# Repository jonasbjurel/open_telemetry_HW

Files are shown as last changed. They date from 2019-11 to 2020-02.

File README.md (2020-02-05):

# open_telemetry_HW





**Licenses:**

The official OpenFly Telemetry project(s) are all open source. The licensing may vary from GPL 2, GPL 3, Apache, or Creative Commons. As with many other hardware projects – OpenFly Telemetry comes with the Creative Commons - CC BY 2.0 license.

**Disclaimers:**

The use of any HW, SW or instructions from the OpenFly Telemetry open source project, or any references to other art - is at your own risk. No warranties, or legal obligations shall be assumed from the creators – in any way. Flying model planes, drones or other remotely controlled vehicles always impose danger to the surroundings – make all necessary precautions to make sure that no one is in danger even in case the control of your model is lost for whatever reason.

# Latest news
OFT001v1P1A* with sample BIST SW have declared it's first release candidate February 04 - 2020. First prototype full release is expected during February 2020. See the Wiki for mor information: https://github.com/jonasbjurel/open_telemetry_HW/wiki

# WIKI
 https://github.com/jonasbjurel/open_telemetry_HW/wiki

# OpenFly Telemetry overview
OpenFly Telemetry is an open source project aiming to provide telemetry and navigation capabilities for model airplanes and drones through open source hardware and software. It uses various on-board sensor capabilities such as GPS, Accelerometers, Gyroscopes, Magnetometers, Pitot tubes, temperature sensors, battery voltage and current sensors, RPM sensors, etc. to provide the operator or algorithms with data for manual or automated corrective actions. The algorithms are some time autonomous and resides in the model, are sometimes on ground with the receiver or nearby connected devices or are sometimes even in distant clouds.
The OFT modules can also be placed in the module bay of the transmitter to enrich the transmitter awareness, e.g. Position, direction and additional communication capabilities such as Bluetooth and WIFI conectivity.
 
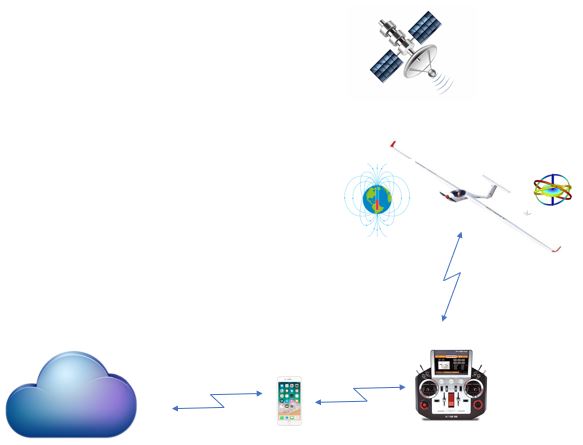
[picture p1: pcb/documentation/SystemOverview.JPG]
OpenFly Telemetry basic idea


**Figure 1:** OpenFly Telemetry basic idea

# OpenFly Telemetry (OFT) system description
OFT has two basic components: the Ada fruit ESP32 Huzzah feather processor board and the OFT system board. The ESP32 processor board obviously holds the software and algorithms for telemetry and navigation. The system board interfaces with the radio receiver and its telemetry and servo busses. The system is modular, and you can compose your choice of capabilities by stacking various OFT sensor boards on top of each other.

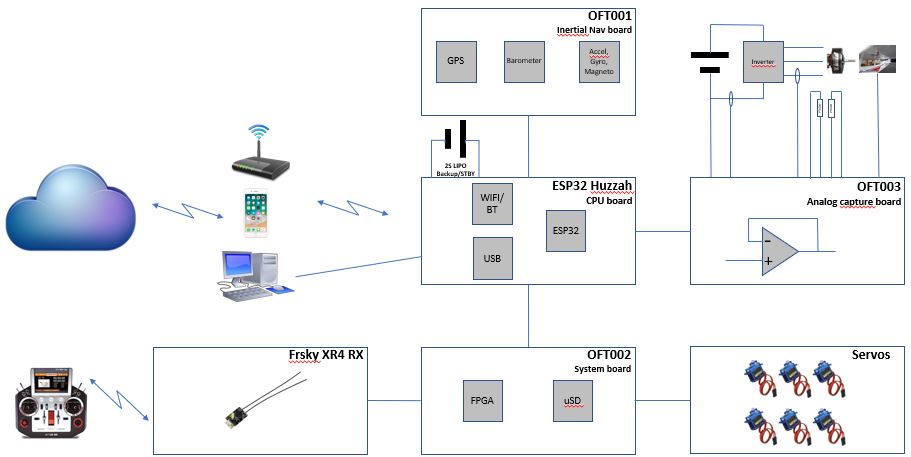
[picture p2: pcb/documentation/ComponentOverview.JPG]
OpenFly Telemetry system view


**Figure 2:** OpenFly Telemetry system view

OFT is based out of the Ada fruit ESP32 Huzzah feather processor board. This board hosts an ESP32 processor with two 32-bit general processor cores, 2 float processors and one ultra-low-power co-processor from Espressif (https://www.espressif.com/). Furthermore, the ESP32 board provides wireless connectivity through Bluetooth and WIFI as well as ensuring continuous power supply through an optional 2S designated LIPO, which could temporarily feed the servos and the receiver- should the main supply drain.
The ESP32 mother board connects to several telemetry acquisition boards in mother-daughter board/shield configurations.

Ada fruit ESP32 Huzzah feather board

**Figure 3:** Ada fruit ESP32 Huzzah feather board

For the on-board use cases (as opposed to the TX bay use case), the bottom most shield in the stack holds the OFT System board. The system board has an FPGA that connects to the radio receiver through the S.PORT for telemetry data, and the SBUS for servo output. The FPGA will allow the ESP32 processor to mix in servo corrections from the processor, transmitting upstream telemetry data, as well as receiving upstream telemetry and servo information from the transmitter. 
The system board interconnects with the radio control receiver through its S.PORT and SBUS.

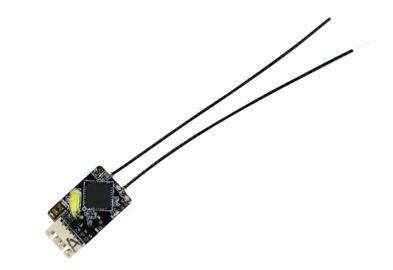
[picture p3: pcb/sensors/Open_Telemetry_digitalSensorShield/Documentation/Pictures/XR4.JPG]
Frsky XR4


**Figure 4:** Frsky XR4 2.4 GHz MIMO CDMA receiver with S.PORT- (telemetry) and SBUS (Servos) connections

# OpenFly Telemetry resources
## OpenFly Telemetry repositories
[OpenFly Telemetry main applications repository](https://github.com/jonasbjurel/open_telemetry)
This repository provides the application software repository for the OpenFly Telemetry project.

[OpenFly Telemetry hardware repository](https://github.com/jonasbjurel/open_telemetry_HW)
The repository for this project - providing HW blue-prints and designs for OpenFly Telemetry.

##  OpenFly Telemetry Dependencies
[ESP32 Arduino](https://github.com/espressif/arduino-esp32)
The Arduino port of Espressif ESP32.

[ESP32 FreeRTOS port documentation](https://docs.espressif.com/projects/esp-idf/en/latest/api-reference/system/freertos.html) FreeRTOS APIs and methods available for ESP32

[High availability- and embedded system FreeRTOS  shim layer](https://github.com/jonasbjurel/coreNoStopRTOS)
System initialization, process monitoring, memory management, system bus arbitration, inter process communication, and much more..

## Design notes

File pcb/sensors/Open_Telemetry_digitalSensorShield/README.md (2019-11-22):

# OFT001v1 Inertial navigation board 
The OFT001v1 Inertial navigation board captures navigational data, such as GPS positioning, 3D acceleration data, 3D Gyroscopic data, 3D Magnetic data, Barometric pressure, Temperature and Humidity. Those data are provided to the ESP32 processor card (and any other shield cards) through I2C and RS232. The data will be filtered, processed and transferred by the ESP32 card and the OFT System card FPGA. It is still to be seen if we can/will implement a high-performance Inertial navigation fuse fixed point Kalman filter in the FPGA, or if it is better done in SW?

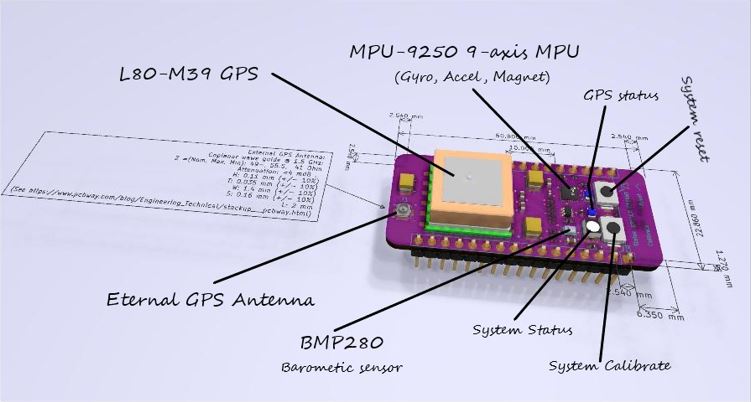
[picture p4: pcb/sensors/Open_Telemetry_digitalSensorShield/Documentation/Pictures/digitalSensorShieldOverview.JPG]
OFT001v1 Inertial navigation card overview

 
**Figure 5:** OFT001v1 Inertial navigation card overview

The OFT001v1 card has an L80-M39 GPS with a built-in patch antenna, and an optional connector for an external 50 Ohm active antenna; an MP-9250 3D axis for each of: Accelerometer, Gyroscope and Magnetometer; and a BMP280 Barometric pressure- humidity- and temperature sensor. Note that the axise's for the acelerometers and Gyrometers differs from those of the manetometers (x swaped with y, and neative Z), clearly marked on the board. The communication with these sensors have been segmented so that the MPU runs on its own high speed I2C channel, allowing fast updates, Kalman filtering-, integration- and Quaternion calculation cycles by the CPU (and possibly later offloaded by the OFT System card FPGA); the BMP280 is less latency critical, and shares an I2C channel with potentially other devices in the stack; while the GPS communication happens over an RS232 serial channel using extensions of the NMEA protocol.

There is one green LED indicator for GPS lock, one orange LED indictor for External GPS antenna use, and an RGB LED for generic system status indication driven from the ESP32 CPU board. There are also two push buttons: one which is connected to the overall system reset, and another multi-purpose push button intended for system calibration activities.

It is important that OFT001v1 sits on the top of the mother-daughter board stack (unless an external GPS antenna is used) in order to achieve a good GPS signal.
Cupper layers have been kept out from ESP32 Bluetooth and WIFI PCB antennas to not deteriorate the signal strength from those.

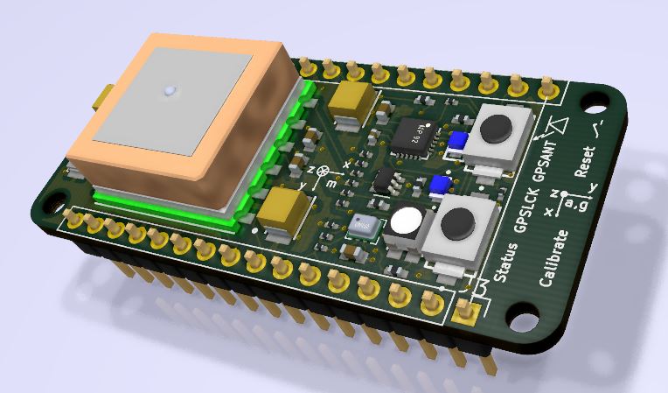
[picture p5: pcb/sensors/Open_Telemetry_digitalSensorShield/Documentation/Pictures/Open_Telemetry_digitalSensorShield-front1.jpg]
OFT001v1


**Figure 6:** OFT001v1

?
## OFT001v1 shield pin-out

| OFT001 12 pin header (J2) | ESP32 HUZZAH 12 pin header (JP3) | ESP32 silicon | Comments |
|---|---|---|---|
| 1 - N/C | VBAT | - | N/C |
| 2 - N/C | EN | - | N/C |
| 3 - N/C | VBUS | - | N/C |
| 4 – RED LED | IO13_A12 | 13 - IO13/A2_6| Red system status led  |
| 5 – BLUE LED | IO12_A11 | 14 – IO12/A2_5| Blue system status led |
| 6 – GREEN LED | IO27_A10 | 12 – IO27/A2_7| Green system status led|
| 7 - N/C | IO33_A9 | 9 - IO33/A1_5 | N/C |
| 8 - N/C | IO15_A8 | 23 – IO15/A2_3| N/C |
| 9 - N/C | IO32_A7 | 8 – IO32/A1_4 | N/C |
| 10 - N/C | IO14_A6 | 13 – IO14/A2_6| N/C |
| 11 - I2C_0_SCL_3V | SCL | 36 – IO22 | Common non-critical I2C|
| 12 - I2C_0_SDA_3V | SDA | 37 – IO23 | Common non-critical I2C|

**Table 1:** J2 shield pin connector

| OFT001 16 pin header (J3) | ESP32 HUZZAH 16 pin header (JP1) | ESP32 silicon |Comments |
|---|---|---|---|
| 1 – INT_0 | IO21 | 33 - IO21 | Interrupt from MPU9250 |
| 2 - I2C_1_SDA_3V | IO17 | 28 - IO17 | Critical MPU I2C |
| 3 - I2C_1_SCL_3V | IO16 | 27 - IO16 | Critical MPU I2C |
| 4 - N/C | MISO | 31 - IO19 | N/C |
| 5 - N/C | MOSI | 30 - IO18 | N/C |
| 6 - N/C | SCK | 29 - IO5 | N/C |
| 7 - CALIB | A5_IO4 | 26 - IO4/A2_2 | System calibration button |
| 8 - UART_1_CLIENT_RXD | A4_IO36 | 4 - IO36/A1_0 | L8-M39 GPS UART (NMEA) |
| 9 - UART_1_CLIENT_TXD | A3_I39 | 5 – IO39/A1_3 | L8-M39 GPS UART (NMEA) |
| 10 – N/C | A2_I34 | 6 – I34/A1_6  | N/C |
| 11 – N/C | A1_DAC1 | 10 – IO25/DAC1/A2_8| N/C |
| 12 – N/C | A0_DAC2 | 11 – IO26/DAC2/A2_9| N/C |
| 13 - GND | GND | -	 | GND from ESP32 motherboard|
| 14 – N/C | N/C | - | N/C |
| 15 - +3.3V (VDD) | +3.3V | - | 3.3V max 120 mA from ESP32 motherboard (rated for max ???)|
| 16 - RESET | RESET | 3 - EN | 2-Way reset |

**Table 2:** J3 shield pin connector

| OFT001 Ext GPS Ant. (J1) | Comments |
|---|---|
| 1 – AGND | External active GPS antenna ground |
| 2 – EXTANT | External active GPS antenna signal with VDD DC applied for power feed |

**Table 3:** J1 External PS Antenna

## OFT001v1 addressing

| I2CBus | Addr	 | Function | Comments |
|---|---|---|---|
| 0	 | 0x77(0x761) (1) | BME280 | - |
| 1 | 0x68(0x692) (2) | MPU9250  | - |

1)	Alternative address if NULL resistor R4 is mounted (not default)
2)	Alternative address if NULL resistor R7 is mounted (not default)

**Table 4:** OFT001v1 I2C addressing

## OFT001 v1 operating specifications
### Operational conditions:

| Parameter | Nom | Max | Min |
|---|---|---|---|
| Voltage | 3.3 V  | 3.6 V | 3.0 V |
| Current | 30 mA  | 120 mA  | - |
| Power dissipation  | 100 mW | 400 mW  | - |
| Ambient temp | - | 85 degC | -40 degC |

**Table 5:** OFT001v1 Operational conditions

### GPS antenna operational conditions:
The built in GPS patch antenna provides the following characteristics:

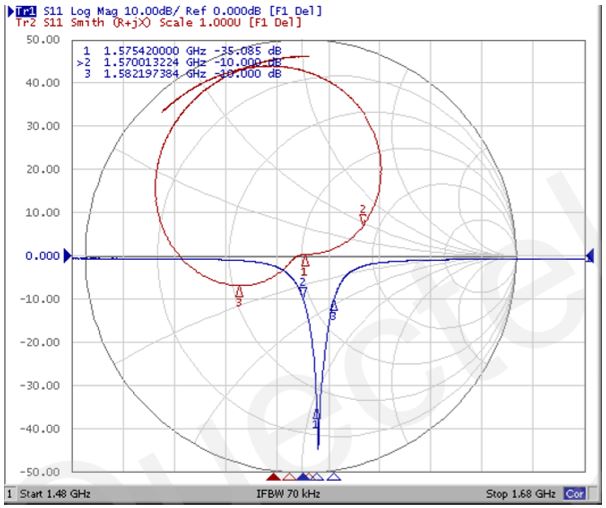
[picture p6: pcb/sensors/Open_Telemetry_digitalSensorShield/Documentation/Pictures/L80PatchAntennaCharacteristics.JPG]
GPS antenna characteristics


**Figure 7:** OFT001v1 Built in L80-M39 path GPS antenna characteristics

External GPS antenna operational requirements:

| Parameter | Value |
|---|---|
| DC feed: | 3.6V – 2.5V |
| DC current (max): | <??? |
| Center frequency: | 1575.42MHz |
| Band width: | >5MHz |
| VSWR: | <2 (Typ.) |
| Polarization: | RHCP or Linear |
| Noise figure: | <1.5dB |
| Gain (antenna): | >-2dBi |
| Gain (embedded LNA): | 20dB (Typ.) |
| Total gain: | >18dBi (Typ.)  |

**Table 6:** OFT001v1 External operational conditions

## OFT001v1 schematics

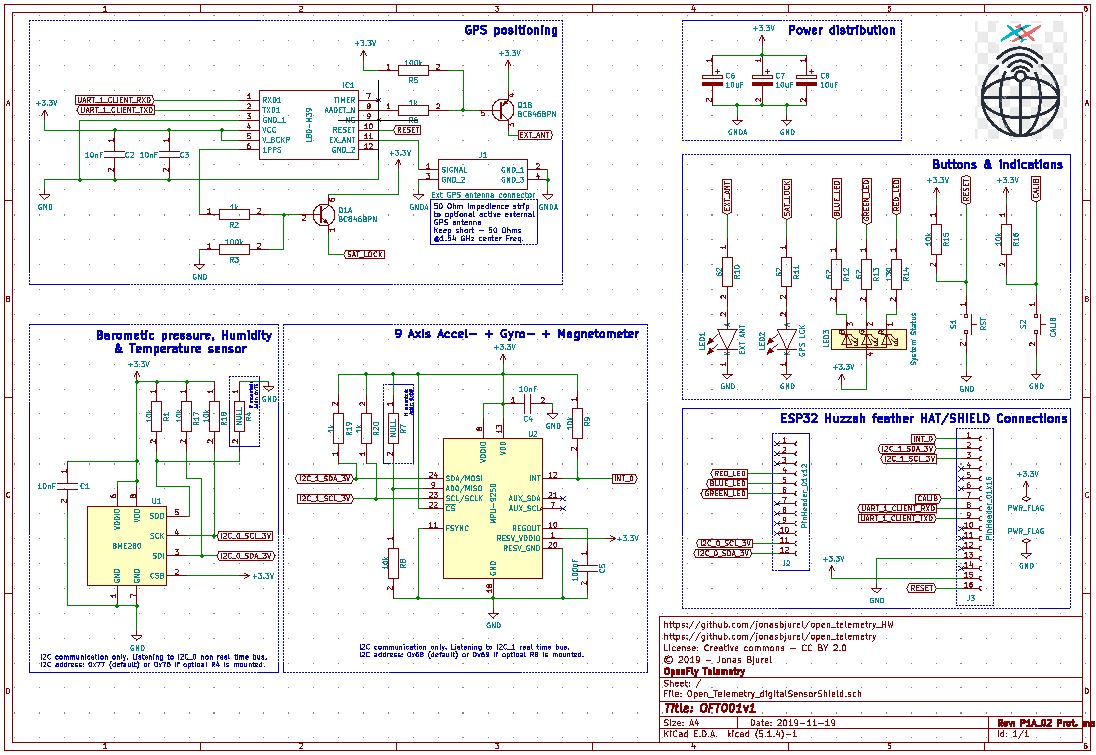
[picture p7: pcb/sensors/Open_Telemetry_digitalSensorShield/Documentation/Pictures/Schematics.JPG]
OFT001v1 schematics

 
**Figure 8:** OFT001v1 schematics

## OFT001v1 - third party data sheets

[L80-M39 GPS receiver](http://docs-emea.rs-online.com/webdocs/147d/0900766b8147dbf2.pdf)

[BME280 Barometric pressure sensor](https://ae-bst.resource.bosch.com/media/_tech/media/datasheets/BST-BME280-DS002.pdf)

[MPU9250 9-Axis Accelerometer, Gyroscope and Magenetometer](http://43zrtwysvxb2gf29r5o0athu-wpengine.netdna-ssl.com/wp-content/uploads/2015/02/PS-MPU-9250A-01-v1.1.pdf)

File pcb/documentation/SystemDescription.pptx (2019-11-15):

## OpenFly Telemetry System description

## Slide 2

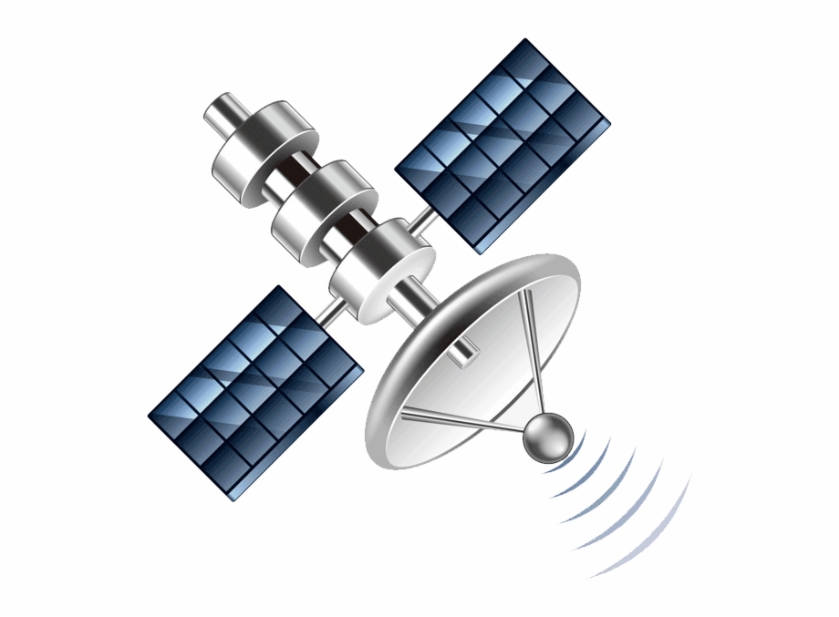
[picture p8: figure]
En bild som visar bord, vit, svart, sitter Automatiskt genererad beskrivning
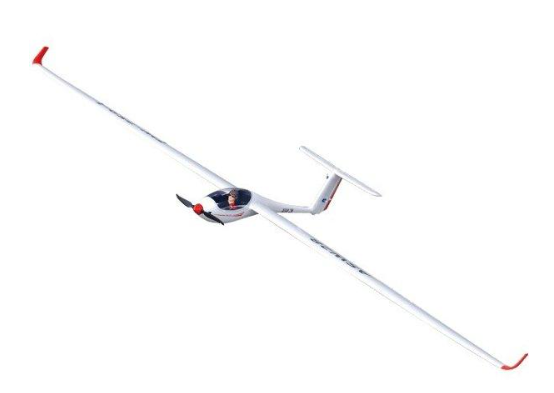
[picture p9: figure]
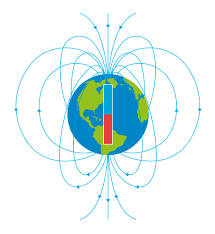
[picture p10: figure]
Image result for earth magnetic field
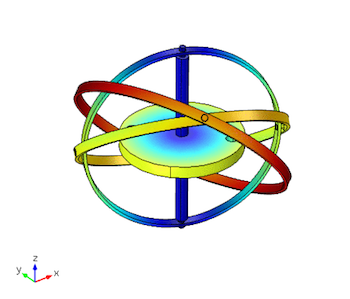
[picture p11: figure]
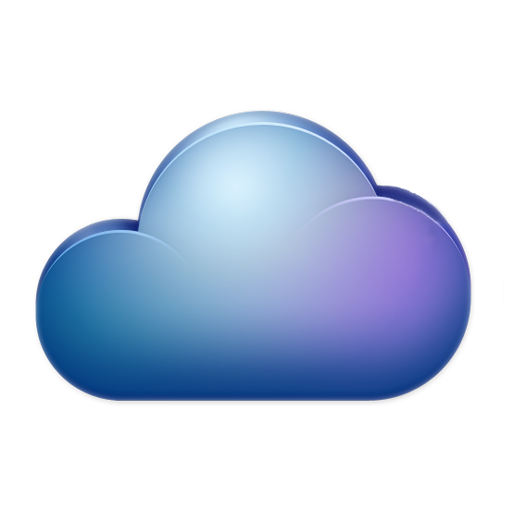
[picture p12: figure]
En bild som visar mus Automatiskt genererad beskrivning
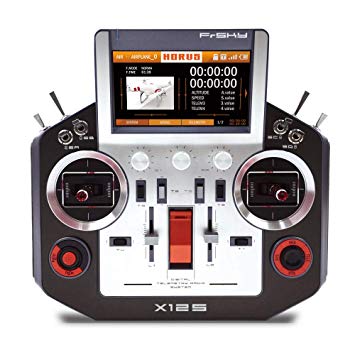
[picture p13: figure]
En bild som visar parkering, gata, sitter, sida Automatiskt genererad beskrivning
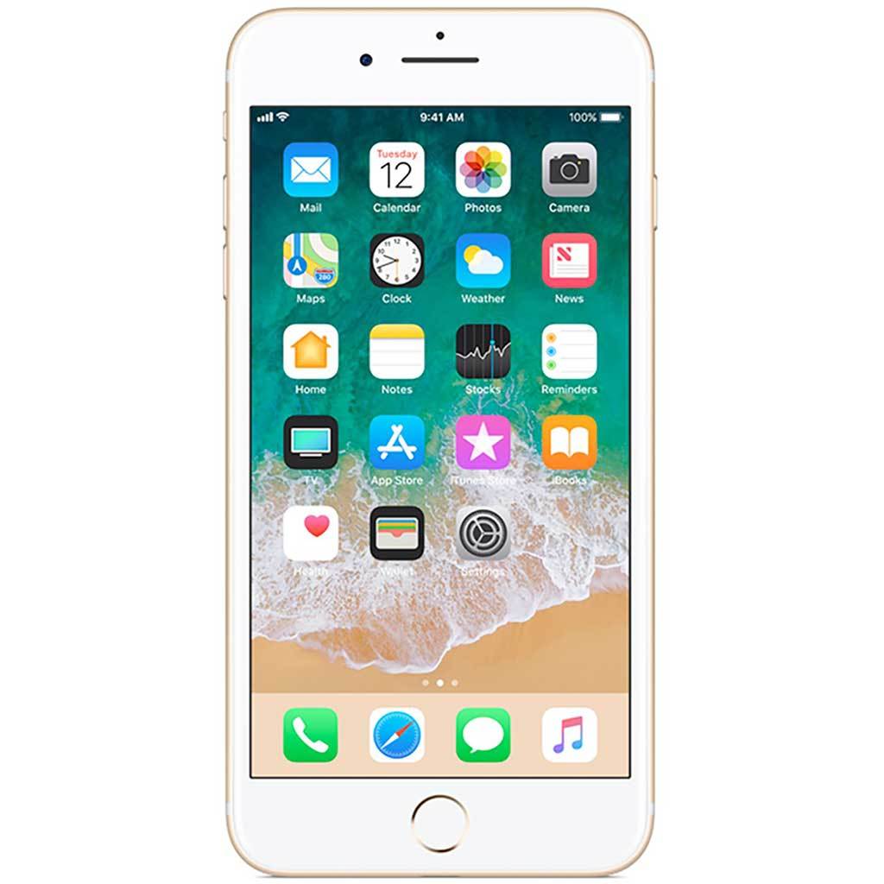
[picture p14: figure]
En bild som visar elektronik, parkering, sitter, mätare Automatiskt genererad beskrivning

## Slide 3

GPS

Barometer

OFT001
Inertial Nav board

Accel,
Gyro,
Magneto

Inverter

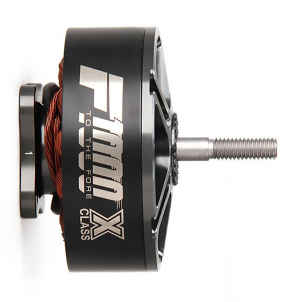
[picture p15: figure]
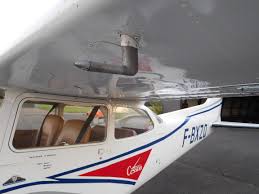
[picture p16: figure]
En bild som visar plan, liten, flygplan, vit Automatiskt genererad beskrivning
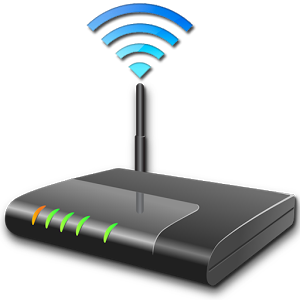
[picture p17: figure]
En bild som visar dator Automatiskt genererad beskrivning

PT1000

PT1000

2S LIPO
Backup/STBY

ESP32 Huzzah
CPU board

OFT003
Analog capture board

WIFI/
BT

ESP32

+

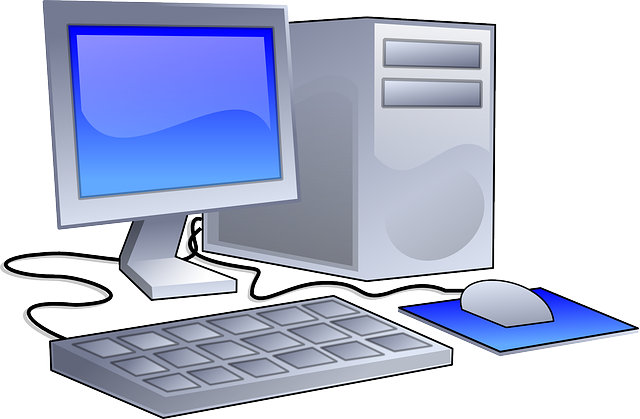
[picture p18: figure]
En bild som visar elektronik, bord, tangentbord, dator Automatiskt genererad beskrivning

USB

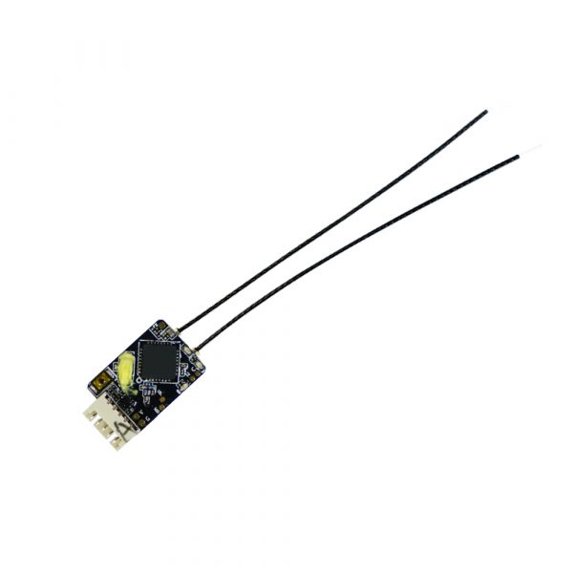
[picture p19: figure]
Image result for frsky xr4 receiver

Frsky XR4 RX

OFT002
System board

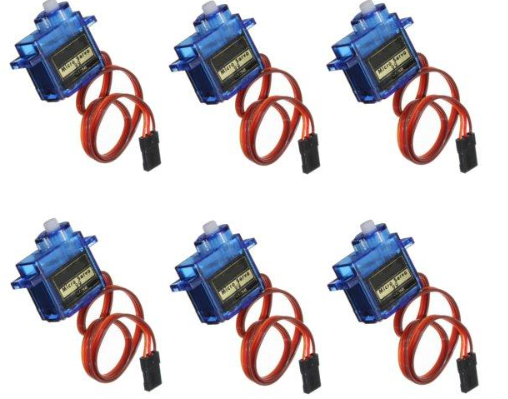
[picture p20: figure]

Servos

FPGA

uSD

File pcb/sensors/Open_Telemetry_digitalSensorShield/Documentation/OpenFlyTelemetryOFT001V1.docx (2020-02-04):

# OpenFly Telemetry © Inertial navigation digital sensor board - OFT001 v1

©2019 Jonas Bjurel

Licenses:
The official OpenFly Telemetry project(s) are all open source. The licensing may vary from GPL 2, GPL 3, Apache, or Creative Commons. As with most hardware projects – such as OFT001 v1, it comes with the Creative Commons - CC BY 2.0 license.

Disclaimers:
The use of any HW, SW or instructions from the OpenFly Telemetry open source project, or any references to other art - is at your own risk. No warranties, or legal obligations shall be assumed from the creators – in any way. Flying model planes, drones or other remotely controlled vehicles always impose danger to the surroundings – make all necessary precautions to make sure that no one is in danger even in case the control of your model is lost for whatever reason.

# Scope

This document describes the OFT001 v1 sensor hardware module part of the OpenFly Telemetry project. OpenFly Telemetry involves several more commercial and proprietary hardware modules which are only to briefly highlighted in this document. The OFT001 v1 boards provides sensor data for inertial navigation such as: GPS data, Barometric data, ambient temperature, 3D accelerometer- , gyrometer-, and 3D magnetometer data.

# OpenFly Telemetry overview

OpenFly Telemetry is an open source project aiming to provide telemetry and navigation capabilities for model airplanes and drones through open source hardware and software. It uses various on-board sensor capabilities such as GPS, Accelerometers, Gyroscopes, Magnetometers, Pitot tubes, temperature sensors, battery voltage and current sensors, RPM sensors, etc. to provide the operator or algorithms with data for manual or automated corrective actions. The algorithms are sometimes autonomous and resides in the model, are sometimes on ground with the receiver or nearby connected devices or are sometimes even in distant clouds.

The OFT modules can also be placed in the module base of the transmitter to enrich the transmitter awareness, e.g. Position, direction and additional communication capabilities such as Bluetooth and WIFI.

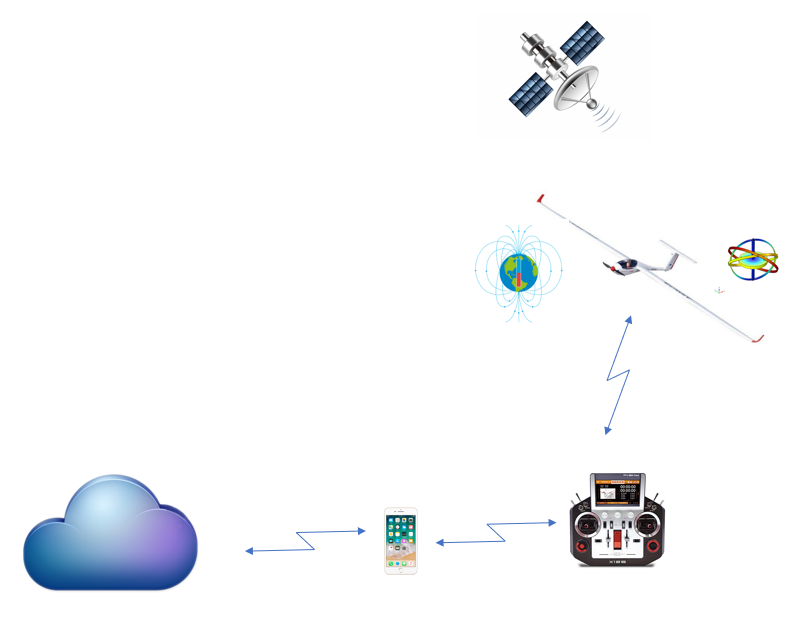
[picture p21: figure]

Figure 1: OpenFly Telemetry basic concept

# OpenFly Telemetry (OFT) system description

OFT has two basic components: the Adafruit Huzzah32 ESP32 feather processor board and the OFT system board. The ESP32 processor board obviously holds the software and algorithms for telemetry and navigation. The system board interfaces with the radio receiver and its telemetry and servo busses. The system is modular, and you can compose your choice of capabilities by stacking various OFT boards on top of each other.

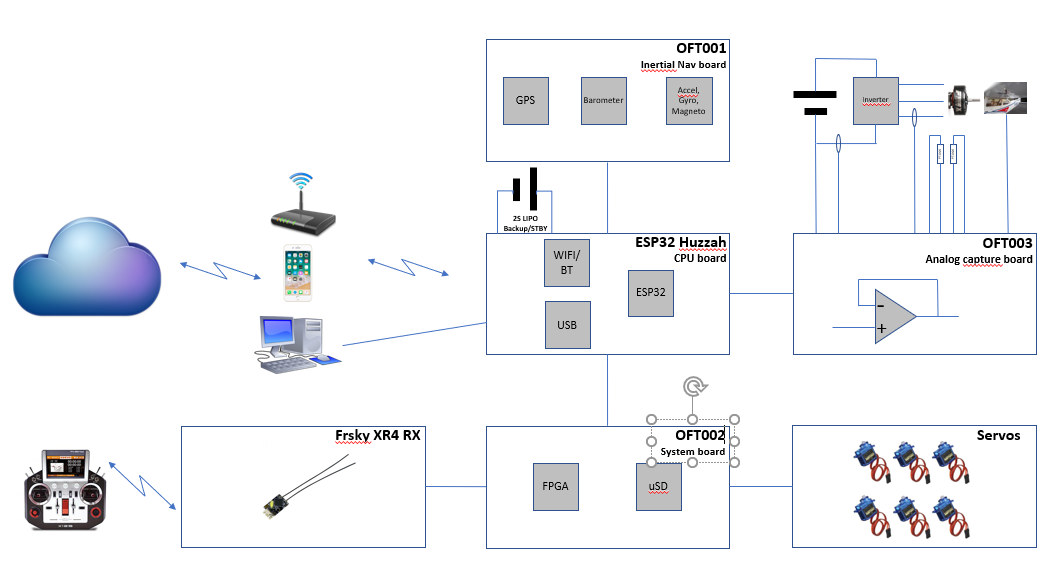
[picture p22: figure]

Figure 2: OpenFly Telemetry system view

OFT is based out of the Ada fruit ESP32 Huzzah feather processor board. This board hosts an ESP32 processor with two 32-bit general Xtensa processor cores, two float processors and one ultra-low-power co-processor from Espressif (https://www.espressif.com/). Furthermore, the ESP32 board provides wireless connectivity through Bluetooth and WIFI as well as ensuring continuous power supply through an optional 2S designated LIPO, which could temporarily feed the servos and the receiver- should the main supply drain.

The commercial Huzzah32 ESP32 mother board connects to several telemetry acquisition boards in mother-daughter board stacked configurations.

Figure 3: Ada fruit ESP32 Huzzah feather board

For the on-board use cases (as opposed to the TX bay use case), the bottom most shield in the stack holds the OFT System board. The system board has an FPGA that connects to the radio receiver through the S.PORT for telemetry data, and the SBUS for servo output. The FPGA will allow the ESP32 processor to mix in servo corrections from the processor, transmitting upstream telemetry data, as well as receiving upstream telemetry and servo information from the transmitter.

The system board interconnects with the radio control receiver through its S.PORT and SBUS.

Image result for frsky xr4 receiver

Figure 4: Frsky XR4 2.4 GHz MIMO CDMA receiver with S.PORT- (telemetry)
and SBUS (Servos) connections

# The OFT001 v1 Inertial navigation board

The OFT001 v1 Inertial navigation board captures navigational data, such as GPS positioning, 3D acceleration data, 3D Gyroscopic data, 3D Magnetic data, Barometric pressure and Temperature. Those data are provided to the Huzzah32 ESP32 processor card (and any other stacked shield cards) through I2C and RS232. The data will be filtered, processed and transferred downstream by the ESP32 card and the OFT System card FPGA. It is still to be seen if we can/will implement a high-performance Inertial navigation fuse fixed point Kalman filter in the FPGA, or if it is better done in SW?

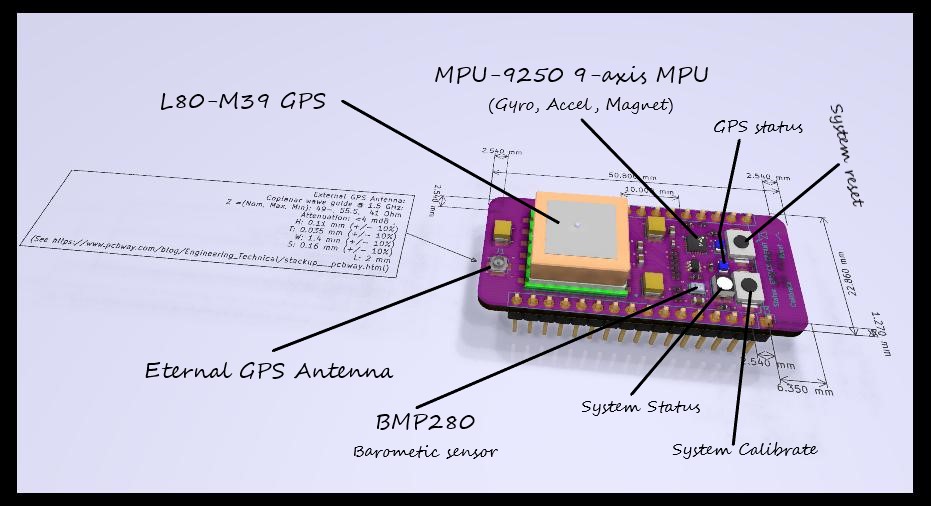
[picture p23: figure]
En bild som visar text Automatiskt genererad beskrivning

Figure 5: OFT001 v1 Inertial navigation card overview

The OFT001 v1 card has an L80-M39 GPS with a built-in patch antenna, and an optional connector for an external 50 Ohm active GPS antenna; an MPU-9250 3D axis Accelerometer, Gyroscope and Magnetometer; and a BMP280 Barometric pressure- and temperature sensor. The communication with these sensors have been segmented so that the MPU runs on its own high speed I²C channel, allowing fast updates and integration cycles by the CPU or possibly directly point to point connection to the OFT System card FPGA; the BMP280 is less latency critical, and potentially shares an I²C channel with other devices in the stack; while the GPS communication happens over an RS232 serial channel using the NMEA protocol.

There is one green LED indicator for GPS lock, one orange LED indictor for External GPS antenna use, and an RGB LED for generic system status indication driven from the ESP32 CPU board. There are also two push buttons: one which is connected to the overall system reset, and another multi-purpose push button intended for system calibration activities.

It is important that OFT001 v1 sits on the top of the mother-daughter board stack (unless an external GPS antenna is used) to achieve a good GPS signal.

Cupper layers have been kept out from the ESP32 Bluetooth and WIFI PCB antennas to not deteriorate the signal strength from those.

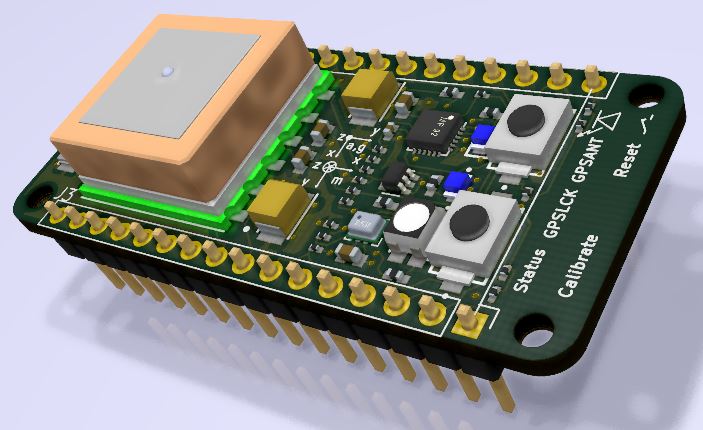
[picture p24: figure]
En bild som visar elektronik, krets Automatiskt genererad beskrivning

Figure 6: OFT001 v1 3D simulation – Front to the right

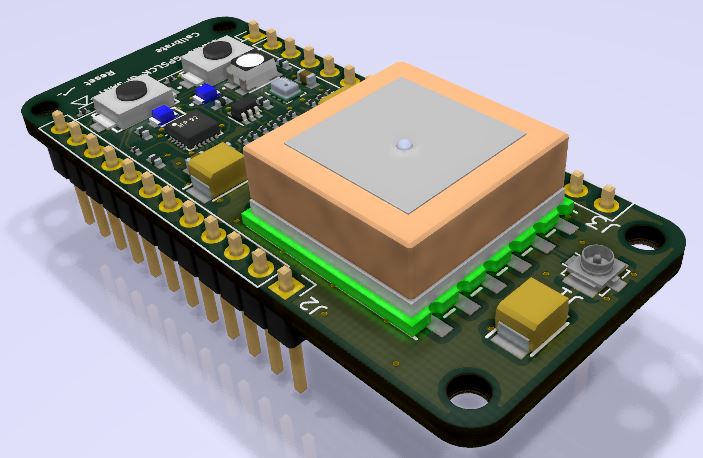
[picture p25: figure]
En bild som visar elektronik, krets Automatiskt genererad beskrivning

Figure 7: OFT001 v1 3D simulation – Front to the upper left

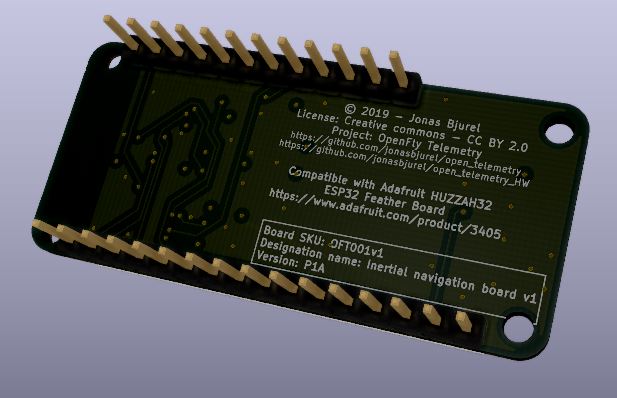
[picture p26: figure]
En bild som visar elektronik, krets Automatiskt genererad beskrivning

Figure 8: OFT001 v1 3D simulation – Back view

## OFT001 v1 pin-out

OFT001 12 pin header (J2) | ESP32 HUZZAH 12 pin header (JP3) | ESP32 silicon | Comments
1 - N/C | VBAT | - | N/C
2 - N/C | EN | - | N/C
3 - N/C | VBUS | - | N/C
4 – RED LED | IO13_A12 | 13 - IO13/A2_6 | Red system status led
5 – BLUE LED | IO12_A11 | 14 – IO12/A2_5 | Blue system status led
6 – GREEN LED | IO27_A10 | 12 – IO27/A2_7 | Green system status led
7 - N/C | IO33_A9 | 9 - IO33/A1_5 | N/C
8 - N/C | IO15_A8 | 23 – IO15/A2_3 | N/C
9 - N/C | IO32_A7 | 8 – IO32/A1_4 | N/C
10 - N/C | IO14_A6 | 13 – IO14/A2_6 | N/C
11 - I2C_0_SCL_3V | SCL | 36 – IO22 | Common non-critical I²C
12 - I2C_0_SDA_3V | SDA | 37 – IO23 | Common non-critical I²C

Table 1: J2 Pin-out

OFT001 16 pin header (J3) | ESP32 HUZZAH 16 pin header (JP1) | ESP32 silicon | Comments
1 – INT_0 | IO21 | 33 - IO21 | Interrupt from MPU9250
2 - I2C_1_SDA_3V | IO17 | 28 - IO17 | Critical MPU I²C
3 - I2C_1_SCL_3V | IO16 | 27 - IO16 | Critical MPU I²C
4 - N/C | MISO | 31 - IO19 | N/C
5 - N/C | MOSI | 30 - IO18 | N/C
6 - N/C | SCK | 29 - IO5 | N/C
7 – CALIB | A5_IO4 | 26 - IO4/A2_2 | System calibration button
~~8 - UART_1_CLIENT_RXD~~ 8 - N/C | A4_IO36 | 4 - IO36/A1_0 | ~~L8~~~~0~~~~-M39 GPS UART (NMEA)~~ Shall not be connected – moved to pin 11, See errata ERROFT001-3
9 - UART_1_CLIENT_TXD | A3_I39 | 5 – IO39/A1_3 | L80-M39 GPS UART (NMEA). Translates to Huzzah32 RXD
10 – N/C | A2_I34 | 6 – I34/A1_6 | N/C
11 – UART_1_CLIENT_RXD | A1_DAC1 | 10 – IO25/DAC1/A2_8 | L80-M39 GPS UART (NMEA) Translates to Huzzah32 TXD
12 – N/C | A0_DAC2 | 11 – IO26/DAC2/A2_9 | N/C
13 – GND | GND | - | GND from ESP32 motherboard
14 – N/C | N/C | - | N/C
15 - +3.3V (VDD) | +3.3V | - | 3.3V max 120 mA from ESP32 motherboard (rated for max ???)
16 – RESET | RESET | 3 – EN | 2-Way reset

Table 2: J3 Pin-out

OFT001 Ext GPS Ant. (J1) | Comments
1 – AGND | External active GPS antenna ground with VDD DC applied for power feed
2 – EXTANT | External active GPS antenna signal with +

Table 3: J1 Pin-out

## OFT001 v1 addressing

I2CBus | Addr | Function | Comments
0 | 0x77 (0x76¹) | BME280
1 | 0x68 (0x69²) | MPU9250

1) Alternative address if NULL resistor R4 is mounted (not default)
2) Alternative address if NULL resistor R7 is mounted (not default)

Table 4: I2C busses and addressing

## OFT001 v1 operating specifications

### Operational conditions:

Parameter | Nom | Max | Min
Voltage | 3.3 V | 3.6 V | 3.0 V
Current | 30 mA + | 120 mA + | -
Power dissipation | 100 mW | 400 mW | -
Ambient temp | - | 85 degC | -40 degC

Table 5: Operating specifications

### GPS antenna operational conditions:

The built in GPS patch antenna provides the following characteristics (probably not really true with the limited ground plane applied!?):

Figure 9: OFT001 v1 built in GPS antenna characteristics

Following external GPS antenna characteristics applies:

Parameter | Value
DC feed: | 3.6V – 2.5V
DC feed current: | <???
Center frequency: | 1575.42MHz
Band width: | >5MHz
VSWR: | <2 (Typ.)
Polarization: | RHCP or Linear
Noise figure: | <1.5dB
Gain (antenna): | >-2dBi
Gain (embedded LNA): | 20dB (Typ.)
Total gain: | >18dBi (Typ.)

Table 6: External GPS antenna operating specifications

## OFT001 v1 P1A schematics

En bild som visar text, karta Automatiskt genererad beskrivning

Figure 10: OFT001 v1 P1A circuit schematics

## OFT001 v1 - third party data sheets

### L80-M39 GPS receiver:

http://docs-emea.rs-online.com/webdocs/147d/0900766b8147dbf2.pdf

BMP280 Barometric pressure sensor:
https://www.bosch-sensortec.com/media/boschsensortec/downloads/datasheets/bst-bmp280-ds001.pdf

### MPU9250 9-Axis Accelerometer, Gyroscope and Magnetometer:

http://43zrtwysvxb2gf29r5o0athu-wpengine.netdna-ssl.com/wp-content/uploads/2015/02/PS-MPU-9250A-01-v1.1.pdf

### TRI-color system status LED:

https://docs.broadcom.com/docs/AV02-4194EN

### GPS status LEDs:

https://docs-emea.rs-online.com/webdocs/156b/0900766b8156b2c9.pdf

## OFT001 v1 PCB implementation

KICAD 5.1.4 has been used to develop the schematics and PCB design. OFT001 v1 relies on a 4-layer FR4 1.6 mm PCB with a minimum of 6 mil inch trace width- and spacing, and a tolerance of 10%. Minimum via drills is 0.3 mm.

### PCB Stack-up

The design is tuned for the PCB stack-up used by PCBway (https://www.pcbway.com/orderonline.aspx)

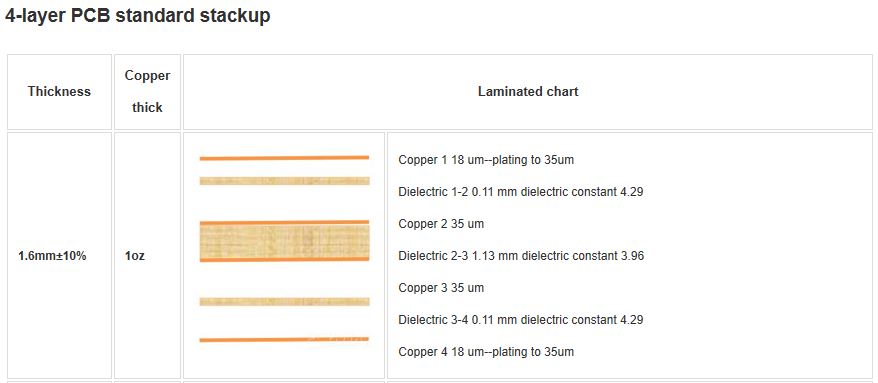
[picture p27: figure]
En bild som visar skärmbild Automatiskt genererad beskrivning

Figure 11: OFT001 v1 – 4-layer PCB stack-up

### Front/top Signal Cupper layer

En bild som visar elektronik Automatiskt genererad beskrivning

Figure 12: OFT001 v1 - Front/top Signal Cupper layer

### Back/bottom Signal CU layer

Figure 13: OFT001 v1 - Back/bottom Signal CU layer

### Top/front embedded GND CU layer

En bild som visar elektronik, krets Automatiskt genererad beskrivning

Figure 14: OFT001 v1 - Top/front embedded GND CU layer

### Back/bottom embedded VDD/3.3V CU layer

En bild som visar elektronik Automatiskt genererad beskrivning

Figure 15: OFT001 v1 - Back/bottom embedded VDD/3.3V CU layer

### Various user technical meta data layers

Figure 16: OFT001 v1 – Various user meta data layers

### External GPS antenna Impedance matching

The external GPS antenna trace needs to be carefully impedance-matched to 50 ohms in order to get the signal losses low and to avoid reflections. Based on PCBWay PCB substrate stack-up, the top cupper strip thickness (T) is estimated to be 35um (+/- 10%), the distance to next ground layer (H) is estimated to be 0.11 mm (+/- 10%), and the dielectric permittivity in between is estimated to be 4.5 F/m @ 1.5 GHz (I need to recalculate with 4.29 F/m Nominal instead).

With the constraints of 6 mil inch strip widths/spacing we end up with a 0.2 mm (W) strip width, and a 6 mil/0.16 mm (S) horizontal spacing to earth - forming a coplanar wave guide with a ground plane of roughly 2 mm length (L) matching the 50 Ohm antenna strip impedance.

En bild som visar elektronik Automatiskt genererad beskrivning

Figure 17: OFT001 v1 – External GPS antenna layout

With this layout, it is expected that the tolerances of non-impedance-controlled PCB manufacturing for this trace stays in between 41-55.5 Ohms, and losses to be less than 10 mdB.

Since the 1.5Ghz GPS wavelength in cupper is roughly 2 dm (100 times the trace length), a few reflections due to impedance matching imperfections should not degrade the antenna signal significantly.

En bild som visar text Automatiskt genererad beskrivning

Figure 18: OFT001 v1 – External GPS antenna layout – top CU layer


Figure 19: OFT001 v1 – External GPS antenna – Impedance calculations

# Appendix A – Huzzah32 commercial mother board reference from Adafruit

OpenFly Telemetry depends on the commercial Adafruit ESP32 Huzzah Feather board as the CPU board. This board is a mandatory part of the OpenFly Telemetry solution, and sits below OFT001v1 in the hardware stack.

This appendix is only for reference, describing the Adafruit ESP32 Huzzah design and pin-out.

Figure 20: Commercial Adafruit ESP32 Huzzah Feather board

En bild som visar text, karta Automatiskt genererad beskrivning

Figure 21: Commercial Adafruit ESP32 Huzzah Feather board schematics

# Appendix B – OFT001 v1 Build of material


Table 7: OFT001 v1 BoM

# Appendix C – OpenFly Telemetry repositories

### OFT HW Repositories:

https://github.com/jonasbjurel/open_telemetry_HW

### OFT SW Repositories:

https://github.com/jonasbjurel/open_telemetry

### OFT SW Plattform Repositories:

https://github.com/jonasbjurel/coreNoStopRTOS

# Appendix D – OFT001v1 Errata/TODOs:

Errata: | Date found: | Products affected: | Versions affected: | Description: | Workaround: | Proposed final fix: | Estimated version for fix: | Concluded final fix
ERROFT001-1 | 2019-12 | OFT001v1 | P1Axx | MPU9250 footprint not optimal | Not needed – successfully mounted | New PCB layout | R1A | Not yet
ERROFT001-2 | 2020-01 | OFT001v1 | P1Axx | High Status diode Luminance | SDK D/A/PWM Trim of Status Luminance | Adjusted LED serial resistors: R12, R13, R14: 330 Ohm | R1A | Not yet
ERROFT001-3 | 2020-01 | OFT001v1 | P1Axx | Erroneous I/O pin assign-ment for GPS UART | Wire patch as described in Appendix D.1 | New PCB layout | R1A | Not yet
Inconclusive | 2020-01 | OFT001v1 | P1Axx | External GPS Antenna not yet validated including the external antenna LED | Inconclusive | Inconclusive | N/A | N/A
Inconclusive | 2020-01 | OFT001v1 | P1Axx | External GPS Antenna trace impedance needs to be re-calculated and validated | Inconclusive | Inconclusive | N/A | N/A

Table 8: OFT001 v1 Errata

# Appendix D.1 – OFT001v1 Errata/TODOs:

## ERROFT001-3:

This workaround is purely limited to the first 5 P1A pre-production boards and should not need to be payed attention to anyone except the creators.

On the front/top layer – solder a wire between L80-M39 Pin #1 and the 16-Pin header Pin#11 and cut the trace between L80-M39 Pin #1 and the 16-Pin header Pin#8 as shown in the picture below.

Figure 22: OFT001 v1 P1A - Front/top signal cupper layer ERROFT001-3 patch

# Appendix E – BIST Self-test software:

The OFT001 v1 comes with a self-test program to validate the functionality of the board. The building and loading of the self-test program is described in Appendix E.1 further down.

The self-test program exercises most of all needed functions in order to validate a functional PCB as well as correct component mounting. Logging and output data are streamed to the standard ESP32 serial output (Serial 0) @ 115.200 baud, as well as to a Bluetooth Low Energy (BLE) virtual serial port. The standard serial port only reports progress-, fault- and debug information; while BLE in addition to that also streams navigational data once the self-test has successfully passed.

The self-test is divided into X phases of testing, whenever a test phase fails – all subsequent test phases are skipped, and the system is halted, showing the fault code for the detected fault.
Following test-phases (in order) are implemented:

CALIB_BUTTON_TEST:
This is the simplest first test, testing the function of calibration. To complete this test, you will need to press the Calibration button within 20 seconds, or the self-test will fail. The Status LED remains entirely unlit during this test phase.

STATUS_LED_TEST:

In this test-phase, the red, blue, and the green LEDs will be calibrated to their respective maximum luminance.

- First the Red color will lit-up, and over time increase its luminance. Press the Calibration button once you’re satisfied with the luminance (don’t go to high in luminance or the LED may be short lived).
- In a second step you will calibrate the blue LED – in this step the red and the blue LED will alternately be lit up – and the red with it calibrated luminance as a reference, and the blue with increasing luminance. Press the Calibration button once the red-, and blue luminance appear to be about the same.
- In a third step you will calibrate the green LED – in this step the red and the green LED will alternately be lit up – and the red with it calibrated luminance as a reference, and the green with increasing luminance. Press the Calibration button once the red-, and green luminance appear to be about the same.

This calibration process will output relative calibration factors for the three status LED colors as a reference for further application development.

The LED calibration will conclude with a status LED color jiggle, leading up to all three emitting at their respective calibrated luminance – appearing as a cold white color if correctly calibrated.

BMP280_TEST

In this phase, the BMP280 Barometric and temperature sensor is discovered through I2C_0. This means that a successful I2C write and read was made to the BMP280 address.
The Status LED remains blue during this test phase.

MPU9250_TEST

In this phase, the MPU-9250 9-Axis Inertial navigation sensor is being discovered through I2C_1. This means that a successful I2C write and read was made to the MPU-9250 address. In additional, the MPU-9250 interrupt line is verified.

The Status LED remains blue during this test phase.

L80M39_TEST

In this phase, the L80-M39 GPS is being discovered. The GPS is being forced into 115200 Baud, and set to report all data points. The reception of data is verified, as well as an order to report the firmware version loaded.

The Status LED remains blue during this test phase.

SUCCESS_TEST

At this point all sensors have successfully been discovered.

Before the coming calibration will start, GPS lock is expected to calibrate GPS altitude to current altitude; if indoors, or otherwise cannot get GPS lock you may press the Calibration button to by-pass GPS altitude calibration, and move on with the rest of the calibrations.

At this point sensor calibration will proceed. When entering this phase, keep the OFT001 v1 board flat, calm and still on a horizontal surface for the accelerometers and gyrometers to successfully calibrate.

When prompted to calibrate the magnetometer, and when status LED turns white – a standard & proprietary calibration scheme is started – wave the sensor board around all 3 axis’s - in all possible angles until the calibration finishes (within one minute).

When the calibration has finished, streaming of sensor data to the BLE device will commence, and the status LED will turn green.

STREAM_SENSORDATA_TEST
Entering the “STREAM_SENSORDATA_TEST” concludes the self-test and the calibration, from here filtered navigation data will be steamed to the BLE device. Example data:
GPS: Date, Time, 2D/3D precision, Acquired Satellites, Lon, Lat, Speed, Hdg, Alt
Barometric: Pressure, Alt, Temp
Inertial (Euler): Pitch, Roll, Yaw, Mag-Hdg, Mag-Inclination, Mag-Field, Total-G

These values are filtered, and for the Inertial Euler angles a software Fuse/Kalman filter is employed.
Some of these measurements have been complemented with its derivates/rates.

The streaming data is only accessible through a BLE serial device.

The Status LED remains green during this test phase.

FAIL_TEST

The self-test has failed in any of its phases. In this condition a fault code will be printed, and the process will spin/halt. Current fault codes are defined:

#define BIST_FC_SUCCESS 0

#define BIST_FC_CALIB_BUTTON_FAIL 1

#define BIST_FC_STATUS_LED_FAIL 2

#define BIST_FC_BPM280_NO_DETECT_FAIL 3

#define BIST_FC_BPM280_DETECT_BUT_NO_FUNCTION_FAIL 4

#define BIST_FC_L80M39_NO_DETECT_FAIL 5

#define BIST_FC_L80M39_DETECT_BUT_NO_FUNCTION_FAIL 6

#define BIST_FC_GPS_NO_1PSS_LOCK_FAIL 7

#define BIST_FC_NO_EXT_ANT_DETECT_FAIL 8

#define BIST_FC_MPU9250_NO_DETECT_FAIL 9

#define BIST_FC_AK8963_NO_DETECT_FAIL 10

#define BIST_FC_MPU9250_DETECT_BUT_NO_FUNCTION_FAIL 10

#define BIST_FC_MPU9250_INTERUPT_LINE_OPEN 11

#define BIST_FC_MPU9250_NO_INTERUPT 12


Figure 23: OFT001 v1 Self-test BLE streaming of navigation data to an Apple IOS device

# Appendix F – Setting up OFT001 v1 design environment for self-test

## Pre-phase

The OFT Software development have so far been using the Visual Studio and Visual Micro components for software development; this is because bare Arduino is to ridge in its way to define dependencies, local libraries, and project file structure including git sub modules etc.

On the other hand – Visual studio with its many project meta files does not easily port to a new environment, even if the same infrastructure (x86, Windows 10, …). Although I have provided some instructions below to build the simplest OFT001 v1 self-test, I’m the first to admit that it is too complicated-, too many manual steps-, to much manual clicks for library dependencies which may go wrong. The best building practice would have been a Linux cross-compiler environment with ordinary make scripts taking care of the dependencies – but we are far from that at this point.

Below is a try to set up the OFT SW environment as been used in the SW development: ….

## Pre-requisites

You need to have a hardware setup stack where there is a Huzzah32 motherboard with stackable connectors connecting to the OFT001 v1 sitting on top of the Huzzah32 board.

You also need to have a Windows computer with a USB interface, and an USB micro-connector connected to the Huzzah32 board for power feed and downloading of the software. This is in practice a USB/Serial converter which requires a very selective driver version – outside the scope of this description.

## Install GIT and appropriate GIT tools

The OFT project uses GIThub (www.github.com) as a global repository, for version control as well as for community collaboration. To be able to pull the repositories needed, as well ass collaborate in the project you need to install a GIT client.

Download and install the “GIT for Windows” client from here: https://git-scm.com/download/win and stay with the default installation settings. This will install a GIT client and a Unix style GIT bash console “Git Bash”.

If you are familiar with GIT and the GIT commands you can stay with “Git for Windows” and “Git Bash”, if not download the “Git Extensions” GUI front-end from here: https://sourceforge.net/projects/gitextensions/ Use default installation settings, except for the SSH client, where you want to use Putty instead of OpenSSL.

You now need to download PUTTY, an open source console, SSH and a SSH key generator, install it from here: https://www.puttygen.com/download-putty
Now run PuTTYGen and press “Generate” button to generate your own private and public SSH key pair:

Figure 24: PuTTYGen - generating your own SSH key pair

After the keys have been generated, save the private and public key to a safe place on your local disk: [file, save public key] and [file, save private key].

## Clone the OpenFlight Telemetry HW repository

Open Git Extensions previously installed, select “Clone repository” from the upper left corner.

Figure 25: GIT Extensions, cloning a github repository

TODO – SSH KEY MANAGEMENT?

Now a pop-up menu will show up asking you what upstream github cloud repository to clone, where to place it on your local disk, and which branch to clone,

The “upstream repository” shall be: https://github.com/jonasbjurel/open_telemetry_HW.git

The “Destination” shall be a folder/path on your local disk

The “Subdirectory to create” is the sub folder name/path in which the local copy of the repository will be placed.

The “Branch” defines the repository branch to clone, master is an unstable branch – so you better use a release branch such as OFT001V1P1A or as you which.


Figure 26: GIT Cloning of the OFT001 “open_telemetry_HW” repository

You now have the repository cloned to your local disk, with a GIT repository versioning data-base, you may now use standard GIT operations on your local repository such as: editing, staging for commit, committing, interacting with the upstream repository – but this is all outside of this description.

## Installing Visual Studio and Visual Miro Arduino Integrated Development Environment (IDE)

The OFT project is using Visual Studio and Visual Micro for ESP32 Arduino as it’s software development environment. Follow these instructions to install this environment: https://www.visualmicro.com/#
Note: Do not install the Windows App version of the Arduino IDE, but the full download version.

## Open, configure and build the OFT001v1 BIST (Self-test project)

Open “Visual Studio” using “Continue without code” option:

Figure 27: Select “Continue without code”


Figure 28: Under vMicro, select “Configure Arduino IDE Location(s):

In the “Optional additional board urls” field, add: http://arduino.esp8266.com/stable/package_esp8266com_index.json,
https://adafruit.github.io/arduino-board-index/package_adafruit_index.json,
https://dl.espressif.com/dl/package_esp32_index.json

It is important to fill in your local sketchbook location – such that the IDE can find the libraries that comes with the BIST repository. I.e.:
[git-root]\open_telemetry_HW\pcb\sensors\Open_Telemetry_digitalSensorShield\BIST\OFT001v1_BIST


Figure 29: Arduino IDE version, location, board support package URLs and Sketch location

Under “vMicro”, enable the software license (payed or trial).

Under “vMicro”, select the Arduino IDE version you previously installed and under the “Board” option, select “Find or install a board…”


Figure 30: Select “Find or install board …”

Install the latest ESP32 board support package (in this example 1.0.4) and the click on “Rescan” at the top of the screen.

Figure 31: Select latest version of ESP32 IDE

You should now be able to select the “Adafruit ESP32 Feather” board support package under “vMicro” – “Board”.


Figure 32: Select the Adafruit ESP32 feather board support package

Under vMicro, set-up the COM port- and speed for the ESP32 binary upload:


Figure 33: Select the upload COM port and speed

Now load the OFT001v1 self-test project found in your local cloned “open_telemetry_HW” repository, I.e.:
[git root]\pcb\sensors\Open_Telemetry_digitalSensorShield\BIST\OFT001v1_BIST\OFT001v1_BIST.sln and start the build by selecting vMicro -> Build & Upload.

## Bluetooth Low Energy (BLE) monitoring and data-streaming

The BIST self-test status-, events- and navigational data are continuously streamed to Bluetooth Low Energy UART capable client devices. There are many such device Apps for mobile devices for IoS, Android and Windows. The one application which has been mostly used in the OFT hardware development is “AirTerminal” for Apple IOS.

## Pre-build binary download and installation

TODO

Document Id: OFT001V1_DESC Rev: PA8 2 Date: 2020-02-04 Author: Jonas Bjurel OpenFly Telemetry ©

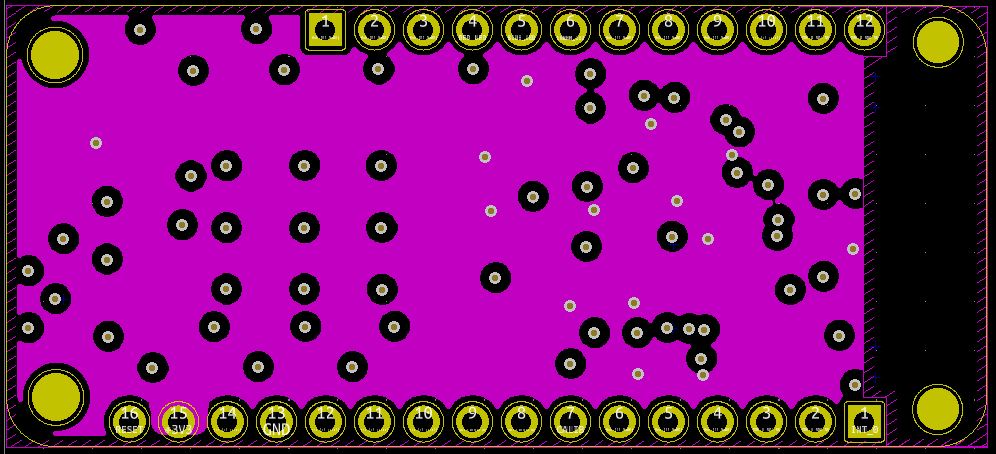
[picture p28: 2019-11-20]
pcb/sensors/Open_Telemetry_digitalSensorShield/Documentation/Pictures/InB.VDD.Cu.JPG

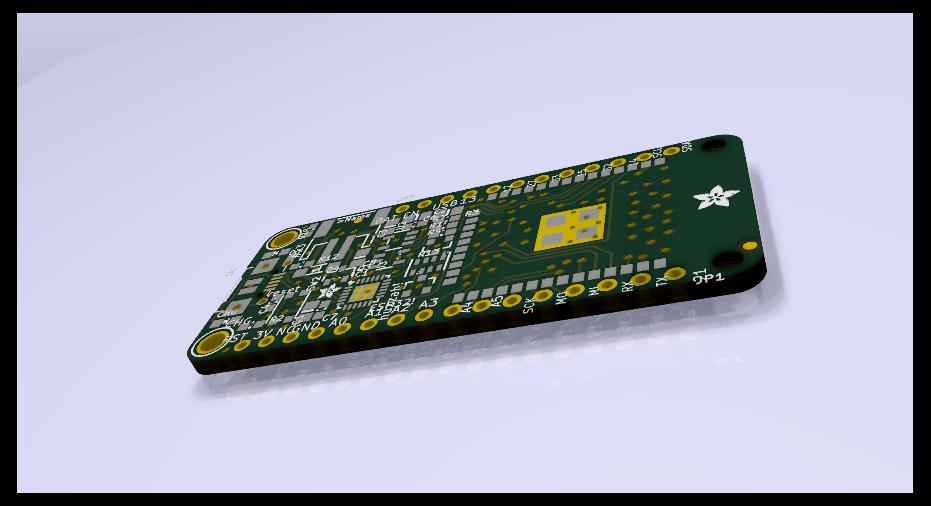
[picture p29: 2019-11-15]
pcb/sensors/Open_Telemetry_digitalSensorShield/Documentation/Pictures/Adafruit HUZZAH32 ESP32 Feather.jpg

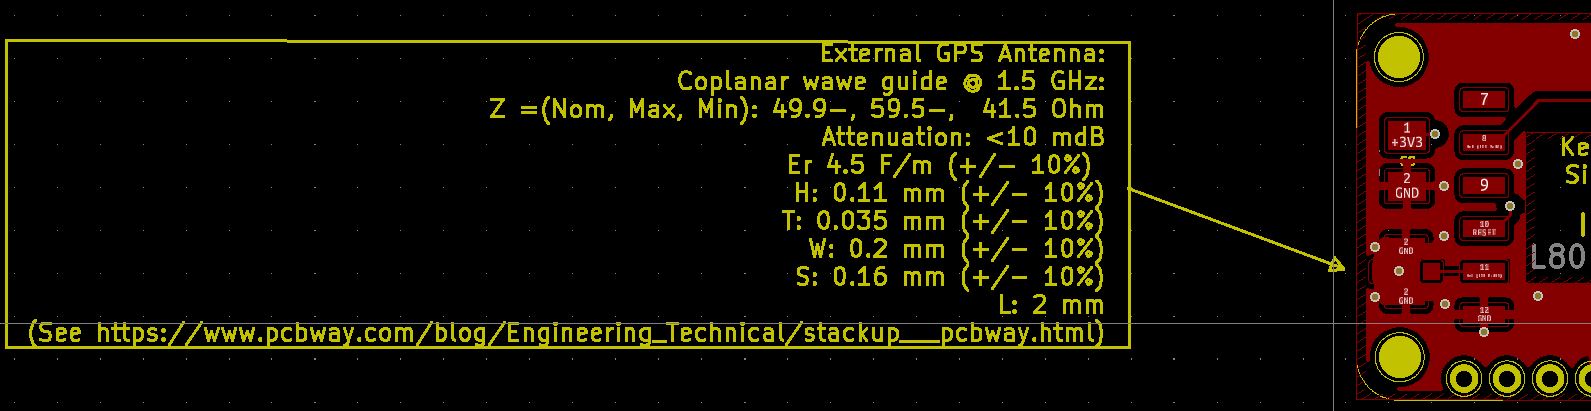
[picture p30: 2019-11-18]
pcb/sensors/Open_Telemetry_digitalSensorShield/Documentation/Pictures/ExtGPSAntenna.JPG

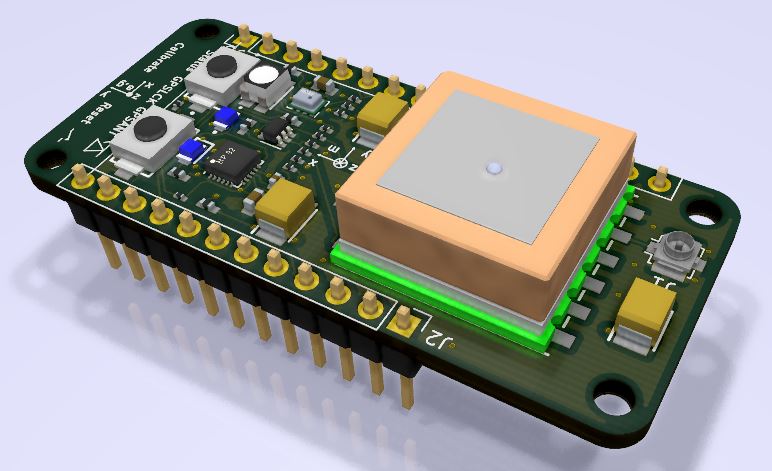
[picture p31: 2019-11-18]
pcb/sensors/Open_Telemetry_digitalSensorShield/Documentation/Pictures/Open_Telemetry_digitalSensorShield-front2.jpg

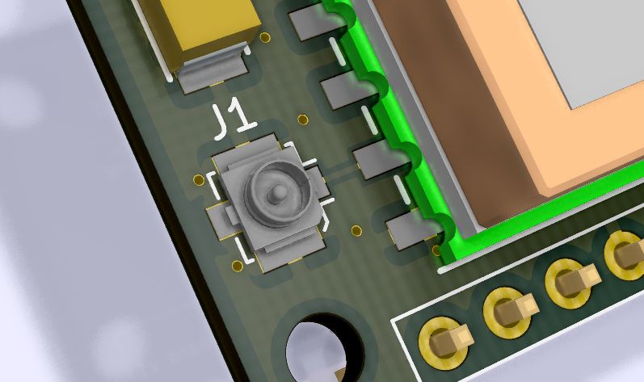
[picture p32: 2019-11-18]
pcb/sensors/Open_Telemetry_digitalSensorShield/Documentation/Pictures/ExtGPSAntennaPCB.JPG

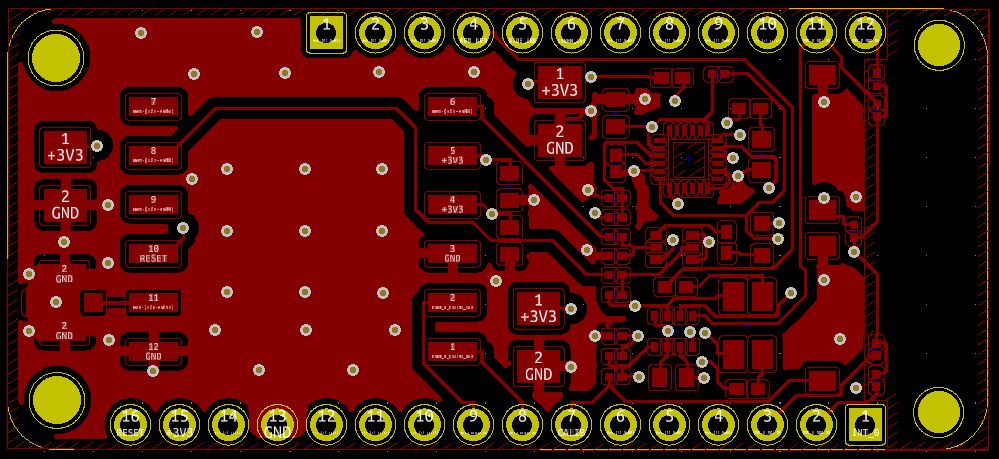
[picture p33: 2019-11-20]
pcb/sensors/Open_Telemetry_digitalSensorShield/Documentation/Pictures/F.Cu.JPG

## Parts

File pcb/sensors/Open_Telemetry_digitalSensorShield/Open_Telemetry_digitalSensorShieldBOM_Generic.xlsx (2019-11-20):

Reference: OpenFly Telemetry - OFT001v1 P1A_BOM Rev.:P1A_02
Item # | Ref Des | Qty | Manufacturer | Mfg Part # | Description / Value | Package | Type | Footprint | Datasheet | Stock price quote source | Stock Price singeltons (Eur) | Sub total Stock Price (Eur)
1 | C1, C2, C3, C4 | 4 | Kemet | C0603C103K4RACTU | CAP, 0.01F, 16V, 10%, X7R | 0603 | SMD | Open_Telemetry:CAPC1608X87N | https://api.kemet.com/component-edge/download/datasheet/C0603C103K4RACTU.pdf | https://www.mouser.com/Search/Refine.aspx?Keyword=80-C0603C103K4R | 0.09 | 0.36
2 | C5 | 1 | Kemet | C0402C104M8RACTU | CAP, 0.1uF, 10V, 20%, X7R | 0402 | SMD | Open_Telemetry:CAPC1005X55N | https://content.kemet.com/datasheets/KEM_C1002_X7R_SMD.pdf | https://www.mouser.com/Search/Refine.aspx?Keyword=80-C0402C104M8R | 0.09 | 0.09
3 | C6, C7, C8 | 3 | Kemet | T491B106K016AT7280 | Tantalum CAP, 10uF, 16V, 10%, ESR=2ohms | 1311 | SMD | CAPPM3528X210N | https://api.kemet.com/component-edge/download/datasheet/T491B106K016AT7280.pdf | https://www.mouser.com/Search/Refine.aspx?Keyword=80-T491B106K16AT7280 | 0.414 | 1.242
4 | IC1 | 1 | Quectel Wireless Solutions | L80-M39 | L80 GPS Module | 12-LCC-2.4mm-16mm | SMD | Open_Telemetry:L80-M39 | http://docs-emea.rs-online.com/webdocs/147d/0900766b8147dbf2.pdf | https://uk.rs-online.com/web/p/products/9084085/ | 12 | 12
5 | J1 | 1 | Molex | 73412-0110 | 50 Ohms, MCRF, PCB Vertical Jack Receptacle | SMT | SMD | Open_Telemetry:U.FL_Molex_MCRF_73412-0110_Vertical | http://www.molex.com/pdm_docs/sd/734120110_sd.pdf | https://www.mouser.com/Search/Refine.aspx?Keyword=538-73412-0110 | 0.63 | 0.63
6 | J2 | 1 | Harwin | M20-9991245 | PinHeader_01x12 2.54 mm pitch | 12 POS | Thru-hole | Open_Telemetry:PinHeader_1x12_P2.54mm_Vertical_Down | https://eu.mouser.com/ProductDetail/Harwin/M20-9991245 | https://eu.mouser.com/ProductDetail/Harwin/M20-9991245 | 0.414 | 0.414
7 | J3 | 1 | Harwin | M20-9991645 | PinHeader_01x16 2.54 mm pitch | 16 POS | Thru-hole | Open_Telemetry:PinHeader_1x16_P2.54mm_Vertical_Down | https://eu.mouser.com/ProductDetail/Harwin/M20-9991645 | https://eu.mouser.com/ProductDetail/Harwin/M20-9991645 | 0.55 | 0.55
8 | LED1 | 1 | ROHM Semiconductor | SML-D13DWT86A | Orange LED | 0603 | SMD | Open_Telemetry:LEDC1608X65N | https://docs-emea.rs-online.com/webdocs/156b/0900766b8156b2c9.pdf | https://www.mouser.com/Search/Refine.aspx?Keyword=755-SML-D13DWT86A | 0.41 | 0.41
9 | LED2 | 1 | ROHM Semiconductor | SML-D13FWT86 | Green LED | 0603 | SMD | Open_Telemetry:SMLD15YWT86 | http://www.rohm.com/web/global/datasheet/SML-D13FW/sml-d13x-e | https://www.mouser.com/Search/Refine.aspx?Keyword=755-SML-D13FWT86 | 0.36 | 0.36
10 | LED3 | 1 | Avago | ASMB-MTB1-0A3A2 | Tricolor black surface RGB surfacce LED | PLCC4 | SMD | Open_Telemetry:AVAGO_PLCC4 | https://docs.broadcom.com/docs/AV02-4194EN | https://eu.mouser.com/ProductDetail/Broadcom-Avago/ASMB-MTB1-0A3A2 | 0.51 | 0.51
11 | Q1 | 1 | Nexperia | BC846BPN, 115 | NPN/PNP transistor | SOT363 | SMD | Package_TO_SOT_SMD:SOT-363_SC-70-6 | https://assets.nexperia.com/documents/data-sheet/BC846BPN.pdf | https://eu.mouser.com/ProductDetail/Nexperia/BC846BPN115?qs=sGAEpiMZZMvaelWNQAznkcopErTqfTCF | 0.29 | 0.29
12 | R1, R8, R9, R15, R16, R17, R18 | 7 | YAGEO (PHYCOMP) | RC0201JR-0710KL | RES, THICK FILM, 10K, 5%, 0.05W | 0201 | SMD | Open_Telemetry:RESC0603X26N | https://www.ttiinc.com/content/ttiinc/en/apps/part-detail.html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 | https://www.mouser.com/Search/Refine.aspx?Keyword=603-RC0201JR-0710KL | 0.09 | 0.45
13 | R2, R6, R19, R20 | 4 | YAGEO (PHYCOMP) | RC0201JR-071KL | RES, THICK FILM, 1K, 5%, 0.05W | 0201 | SMD | Open_Telemetry:RESC0603X26N | https://www.ttiinc.com/content/ttiinc/en/apps/part-detail.html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 | https://www.mouser.com/Search/Refine.aspx?Keyword=603-RC0201JR-071KL | 0.09 | 0.18
14 | R3, R5 | 2 | YAGEO (PHYCOMP) | RC0201JR-07100KL | RES, THICK FILM, 100K, 5%, 0.05W | 0201 | SMD | Open_Telemetry:RESC0603X26N | https://www.ttiinc.com/content/ttiinc/en/apps/part-detail.html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 | https://www.mouser.com/Search/Refine.aspx?Keyword=603-RC0201JR-07100KL | 0.09 | 0.18
15 | R10, R11, R12, R13 | 4 | YAGEO (PHYCOMP) | RC0402JR-0762RL | RES, THICK FILM, 62R, 5%, 0.125W | 0402 | SMD | Open_Telemetry:RESC1005X40N | https://www.ttiinc.com/content/ttiinc/en/apps/part-detail.html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 | https://www.mouser.com/Search/Refine.aspx?Keyword=603-RC0402JR-0762RL | 0.09 | 0.36
16 | R14 | 1 | Vishay | CRCW0402130RJNED | RES,THICK FILM, 130R, 5% 0.063 W | 0402 | SMD | Open_Telemetry:RESC1005X40N | https://www.ttiinc.com/content/ttiinc/en/apps/part-detail.html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 | https://www.mouser.com/Search/Refine.aspx?Keyword=71-CRCW0402130RJNED | 0.09 | 0.09
17 | S1, S2 | 2 | C & K COMPONENTS | KSR223GLFG | RST, CALIB Tactile Switches 1VA, 32VDC, IP50 | SMT | SMD | Open_Telemetry:KSR | https://dznh3ojzb2azq.cloudfront.net/products/Tactile/KSR/documents/datasheet.pdf | https://eu.mouser.com/ProductDetail/CK/KSR223GLFG | 0.828 | 1.656
18 | U1 | 1 | Bosh | BME280 | Barrometic pressure sensor | 2.5mmx2.5mmx093mm metal lid LGA | SMD | Open_Telemetry:Bosch_LGA-8_2x2.5mm_P0.65mm_ClockwisePinNumbering | https://ae-bst.resource.bosch.com/media/_tech/media/datasheets/BST-BME280-DS002.pdf | https://eu.mouser.com/Search/Refine?Keyword=BME280 | 3.36 | 3.36
19 | U2 | 1 | InvenSense | MPU-9250 | 9 Axis MPU | QFN-24_3x3mm | SMD | Open_Telemetry:3DInvenSense_QFN-24_3x3mm_P0.4mm | http://43zrtwysvxb2gf29r5o0athu-wpengine.netdna-ssl.com/wp-content/uploads/2015/02/PS-MPU-9250A-01-v1.1.pdf | https://www.digikey.se/product-detail/sv/tdk-invensense/MPU-9250/1428-1019-1-ND/4626450 | 2.6 | 2.6
DO NOT MOUNT:
20 | R4, R7 | 2 | YAGEO (PHYCOMP) | RC0201JR-070RL | RES, THICK FILM, 0R, 5%, 0.05W | 0201 | SMD | RESC0603X26N | https://www.ttiinc.com/content/ttiinc/en/apps/part-detail.html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 | https://www.mouser.com/Search/Refine.aspx?Keyword=603-RC0201JR-070RL | - | -
Total: | # Unique comp | # Comp. |  |  |  |  | SMD / Thru |  |  |  |  | Tot Stock price
 | 19 | 38 |  |  |  |  | 36/2 |  |  |  |  | 25.732

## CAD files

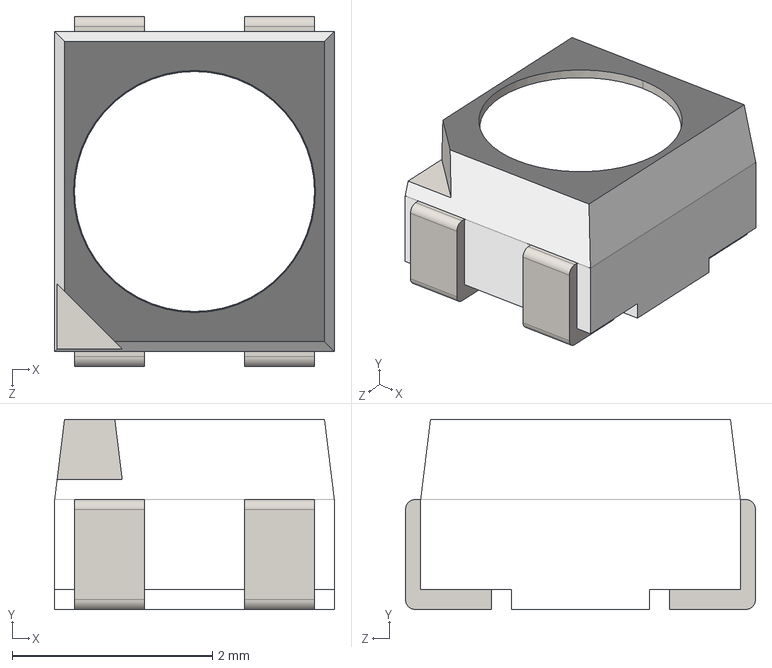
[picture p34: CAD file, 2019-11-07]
pcb/kicadLIB/ASMB-MTB1-0A3A2/3D/User Library-ASMB-MTB0-0A3A2.STEP
2.80 x 1.90 x 3.50 mm

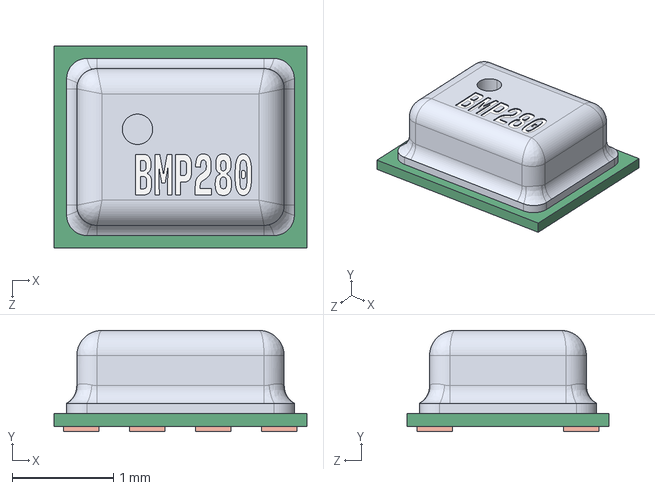
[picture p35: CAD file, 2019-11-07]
pcb/kicadLIB/BMP280/3D/User Library-BST-BMP280.STEP
2.50 x 1.00 x 2.00 mm

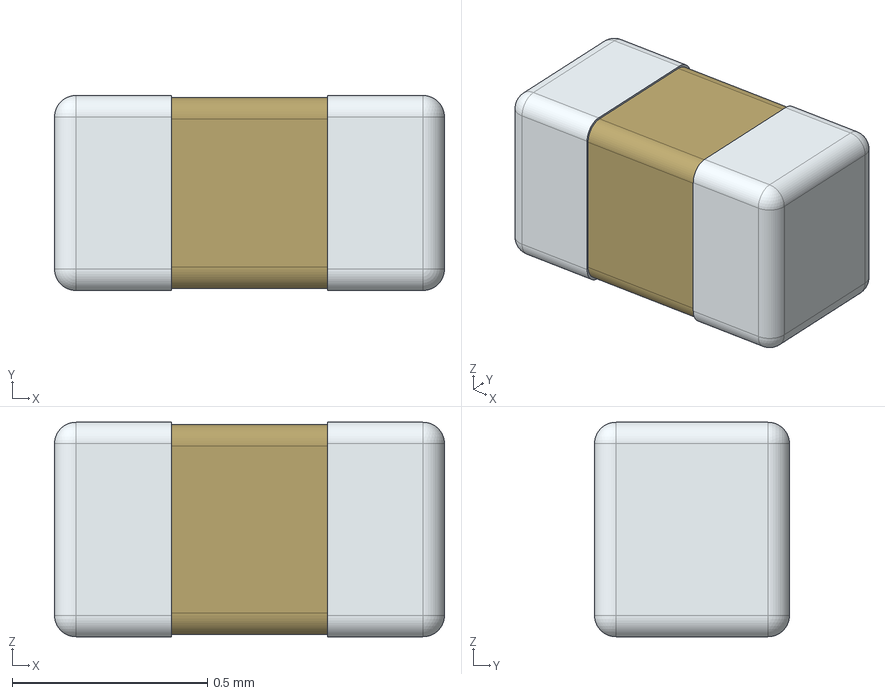
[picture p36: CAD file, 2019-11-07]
pcb/kicadLIB/C0402C104M8RACTU/3D/C0402C104M8RACTU.stp
1.00 x 0.5 x 0.55 mm

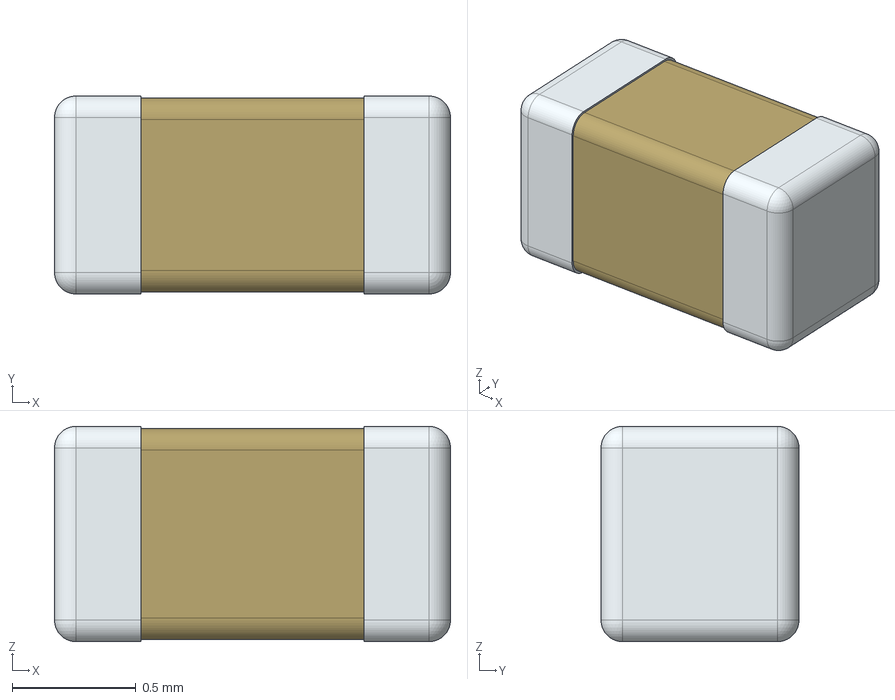
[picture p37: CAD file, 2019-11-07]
pcb/kicadLIB/C0603C103K4RACTU/3D/C0603C103K4RACTU.stp
1.60 x 0.8 x 0.87 mm

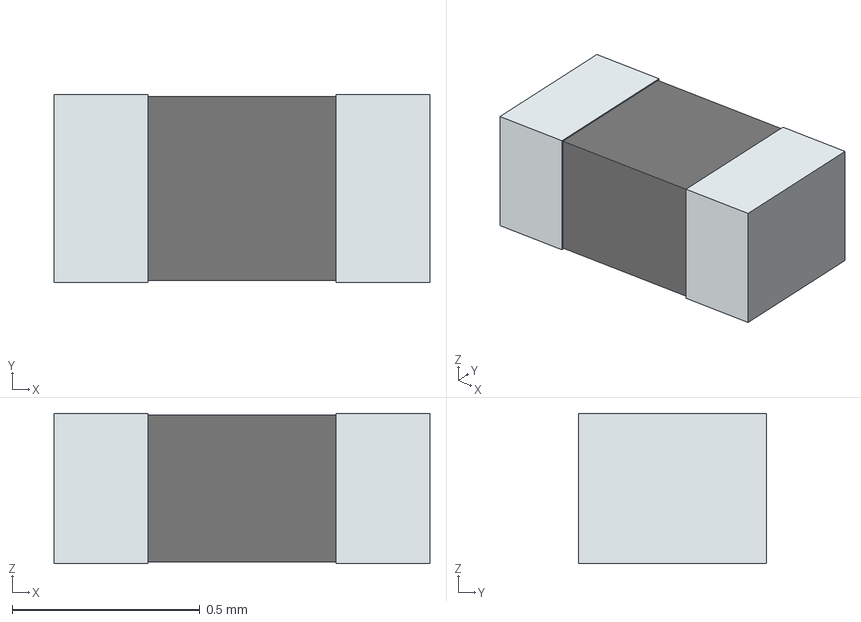
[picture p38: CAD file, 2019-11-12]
pcb/kicadLIB/CRCW0402130RJNED/3D/CRCW0402130RJNED.stp
1.00 x 0.5 x 0.4 mm
term1
term2

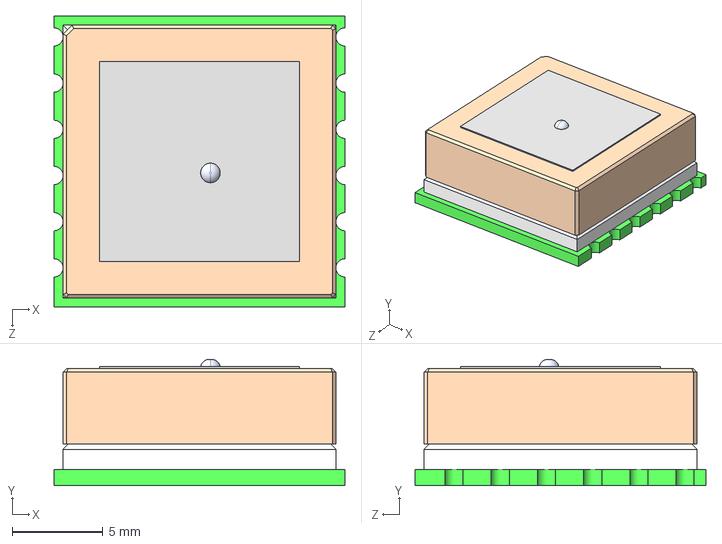
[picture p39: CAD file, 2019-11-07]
pcb/kicadLIB/L80-M39/3D/User Library-quectel-l80.STEP
16.0 x 6.95 x 16.0 mm

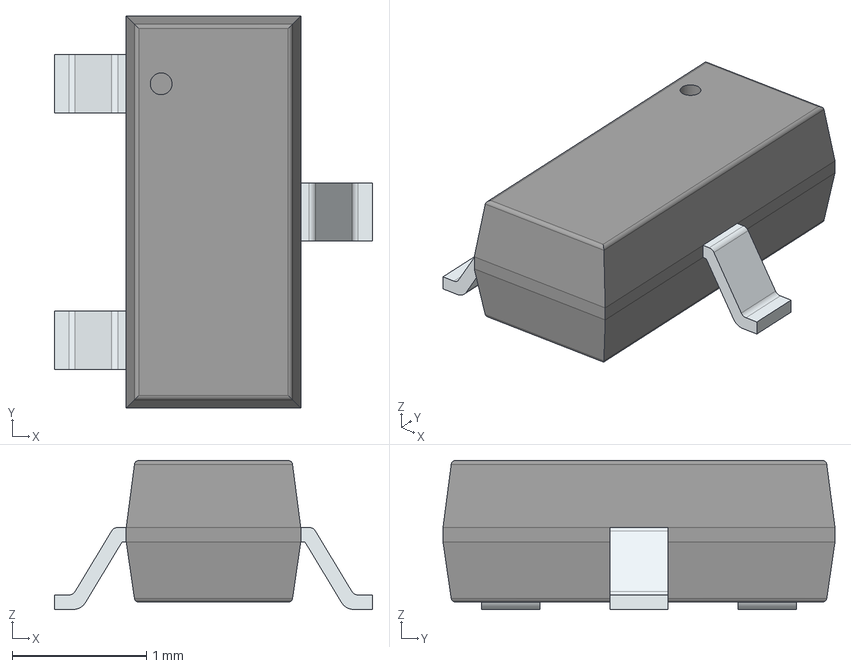
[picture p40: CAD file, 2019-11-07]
pcb/kicadLIB/MMBF4393LT1G/3D/MMBF4393LT1G.stp
2.37 x 2.92 x 1.11 mm
PinsArrayL
FilletPinR

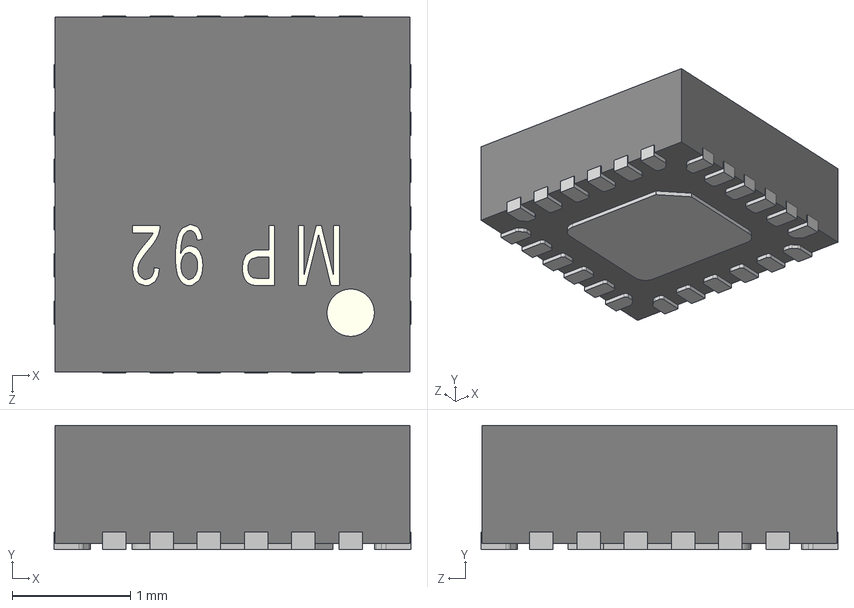
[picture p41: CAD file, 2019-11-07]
pcb/kicadLIB/MPU-9250/3D/User Library-MPU9250.STEP
3.02 x 1.05 x 3.02 mm

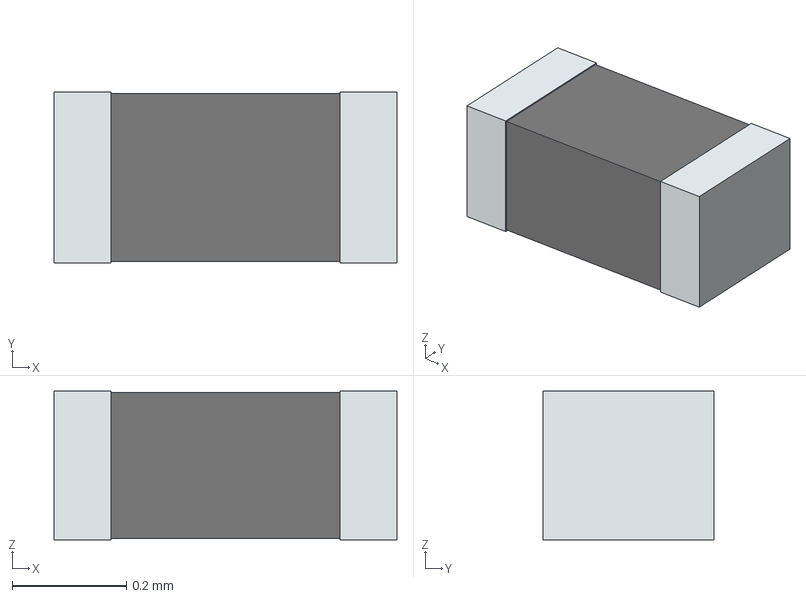
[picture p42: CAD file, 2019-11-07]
pcb/kicadLIB/RC0201JR-070RL/3D/RC0201JR-070RL.stp
0.6 x 0.3 x 0.26 mm
term1
term2

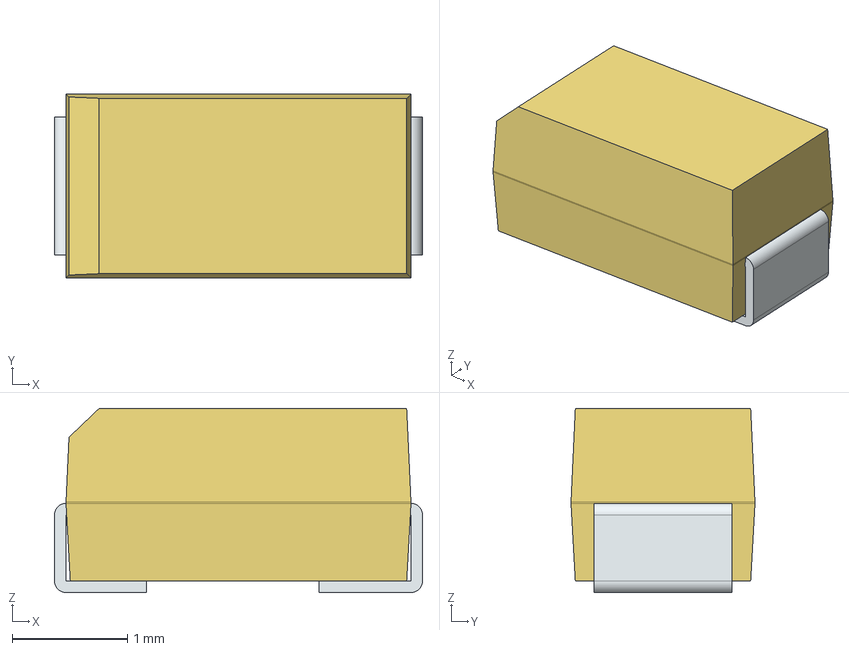
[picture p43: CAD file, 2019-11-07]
pcb/kicadLIB/T491A106M016AT/3D/T491A106M016AT.stp
3.20 x 1.60 x 1.60 mm
FilletPin1
FilletPin2

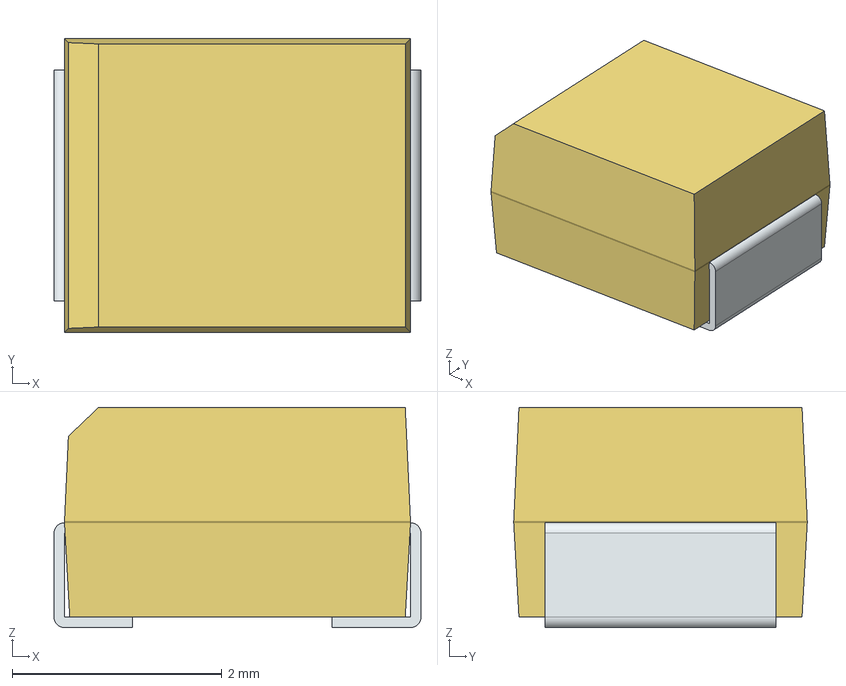
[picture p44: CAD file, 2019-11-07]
pcb/kicadLIB/T491B106K016AT7280/3D/T491B106K016AT7280.stp
3.50 x 2.80 x 2.10 mm
FilletPin1
FilletPin2

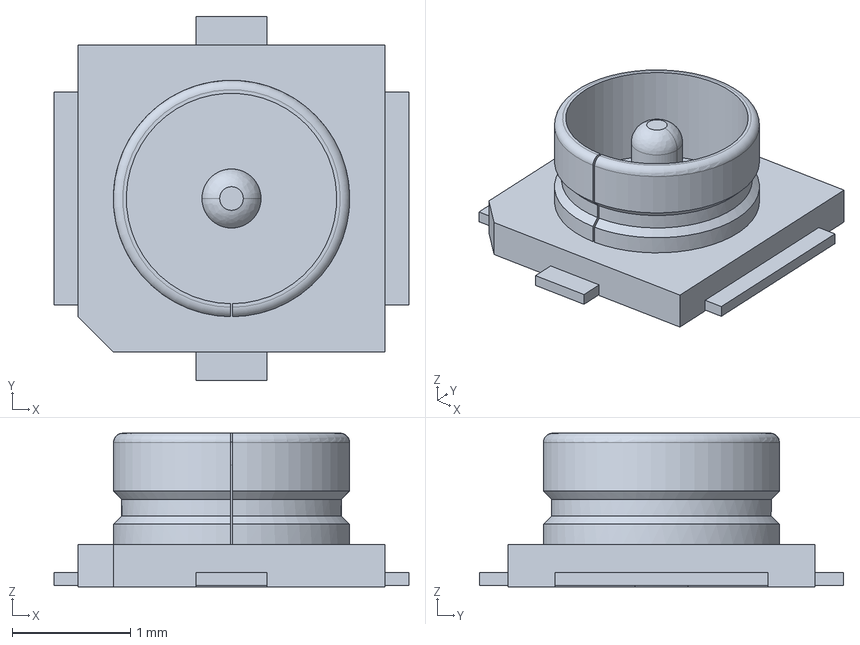
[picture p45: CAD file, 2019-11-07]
pcb/kicadLIB/73412-0110/3D/734120110.stp
3.00 x 3.08 x 1.30 mm

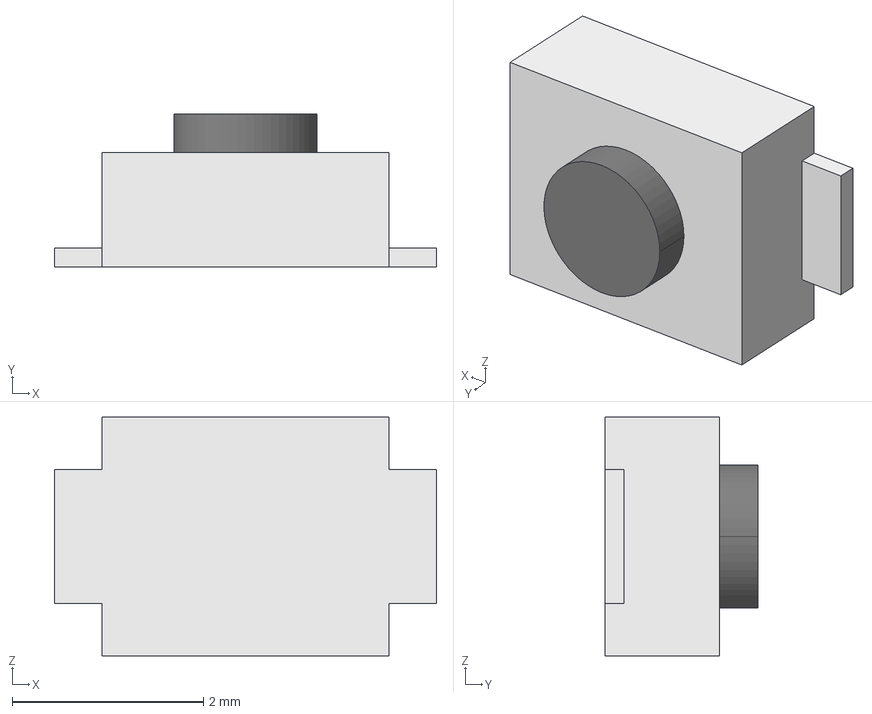
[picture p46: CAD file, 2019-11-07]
pcb/kicadLIB/ATS2D1G_NC_LFS/3D/20041.stp
4.00 x 1.60 x 2.50 mm

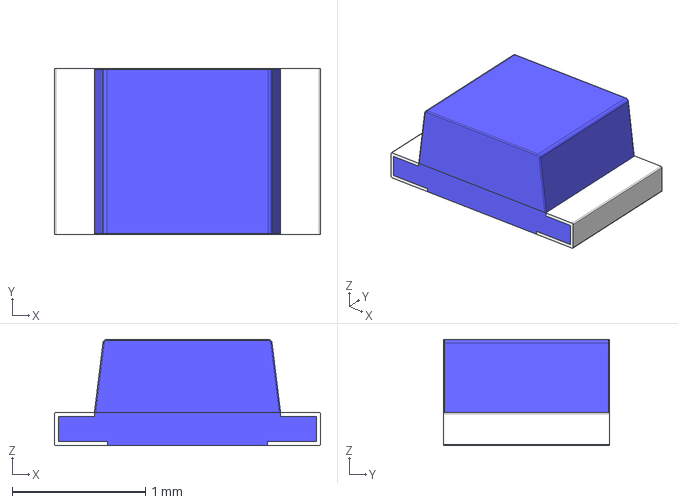
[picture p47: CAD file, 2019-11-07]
pcb/kicadLIB/SML-D13DWT86A/3D/70522027.stp
2.00 x 1.25 x 0.8 mm

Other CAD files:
pcb/kicadLIB/RC0201JR-07100KL/3D/RC0201JR-07100KL.stp
pcb/kicadLIB/RC0201JR-0710KL/3D/RC0201JR-0710KL.stp
pcb/kicadLIB/RC0201JR-071KL/3D/RC0201JR-071KL.stp
pcb/kicadLIB/RC0402JR-0762RL/3D/RC0402JR-0762RL.stp
pcb/kicadLIB/1241.1612.11/Allegro/sms-gullwing.psm
pcb/kicadLIB/1241.1612.11/DEHDL/1241.1612.11/chips/chips.prt
pcb/kicadLIB/73412-0110/Allegro/73412-0110.psm
pcb/kicadLIB/73412-0110/DEHDL/73412_0110/chips/chips.prt
pcb/kicadLIB/ASMB-MTB1-0A3A2/Allegro/avago_plcc4.psm
pcb/kicadLIB/ASMB-MTB1-0A3A2/DEHDL/asmb_mtb1_0a3a2/chips/chips.prt
pcb/kicadLIB/ATS2D1G_NC_LFS/Allegro/ats2d1g.psm
pcb/kicadLIB/ATS2D1G_NC_LFS/DEHDL/ats2d1g_nc_lfs/chips/chips.prt
pcb/kicadLIB/C0402C104M8RACTU/3D/C0402C104M8RACTU.stl
pcb/kicadLIB/C0402C104M8RACTU/Allegro/capc1005x55n.psm
pcb/kicadLIB/C0402C104M8RACTU/DEHDL/c0402c104m8ractu/chips/chips.prt
pcb/kicadLIB/C0603C103K4RACTU/3D/C0603C103K4RACTU.stl
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

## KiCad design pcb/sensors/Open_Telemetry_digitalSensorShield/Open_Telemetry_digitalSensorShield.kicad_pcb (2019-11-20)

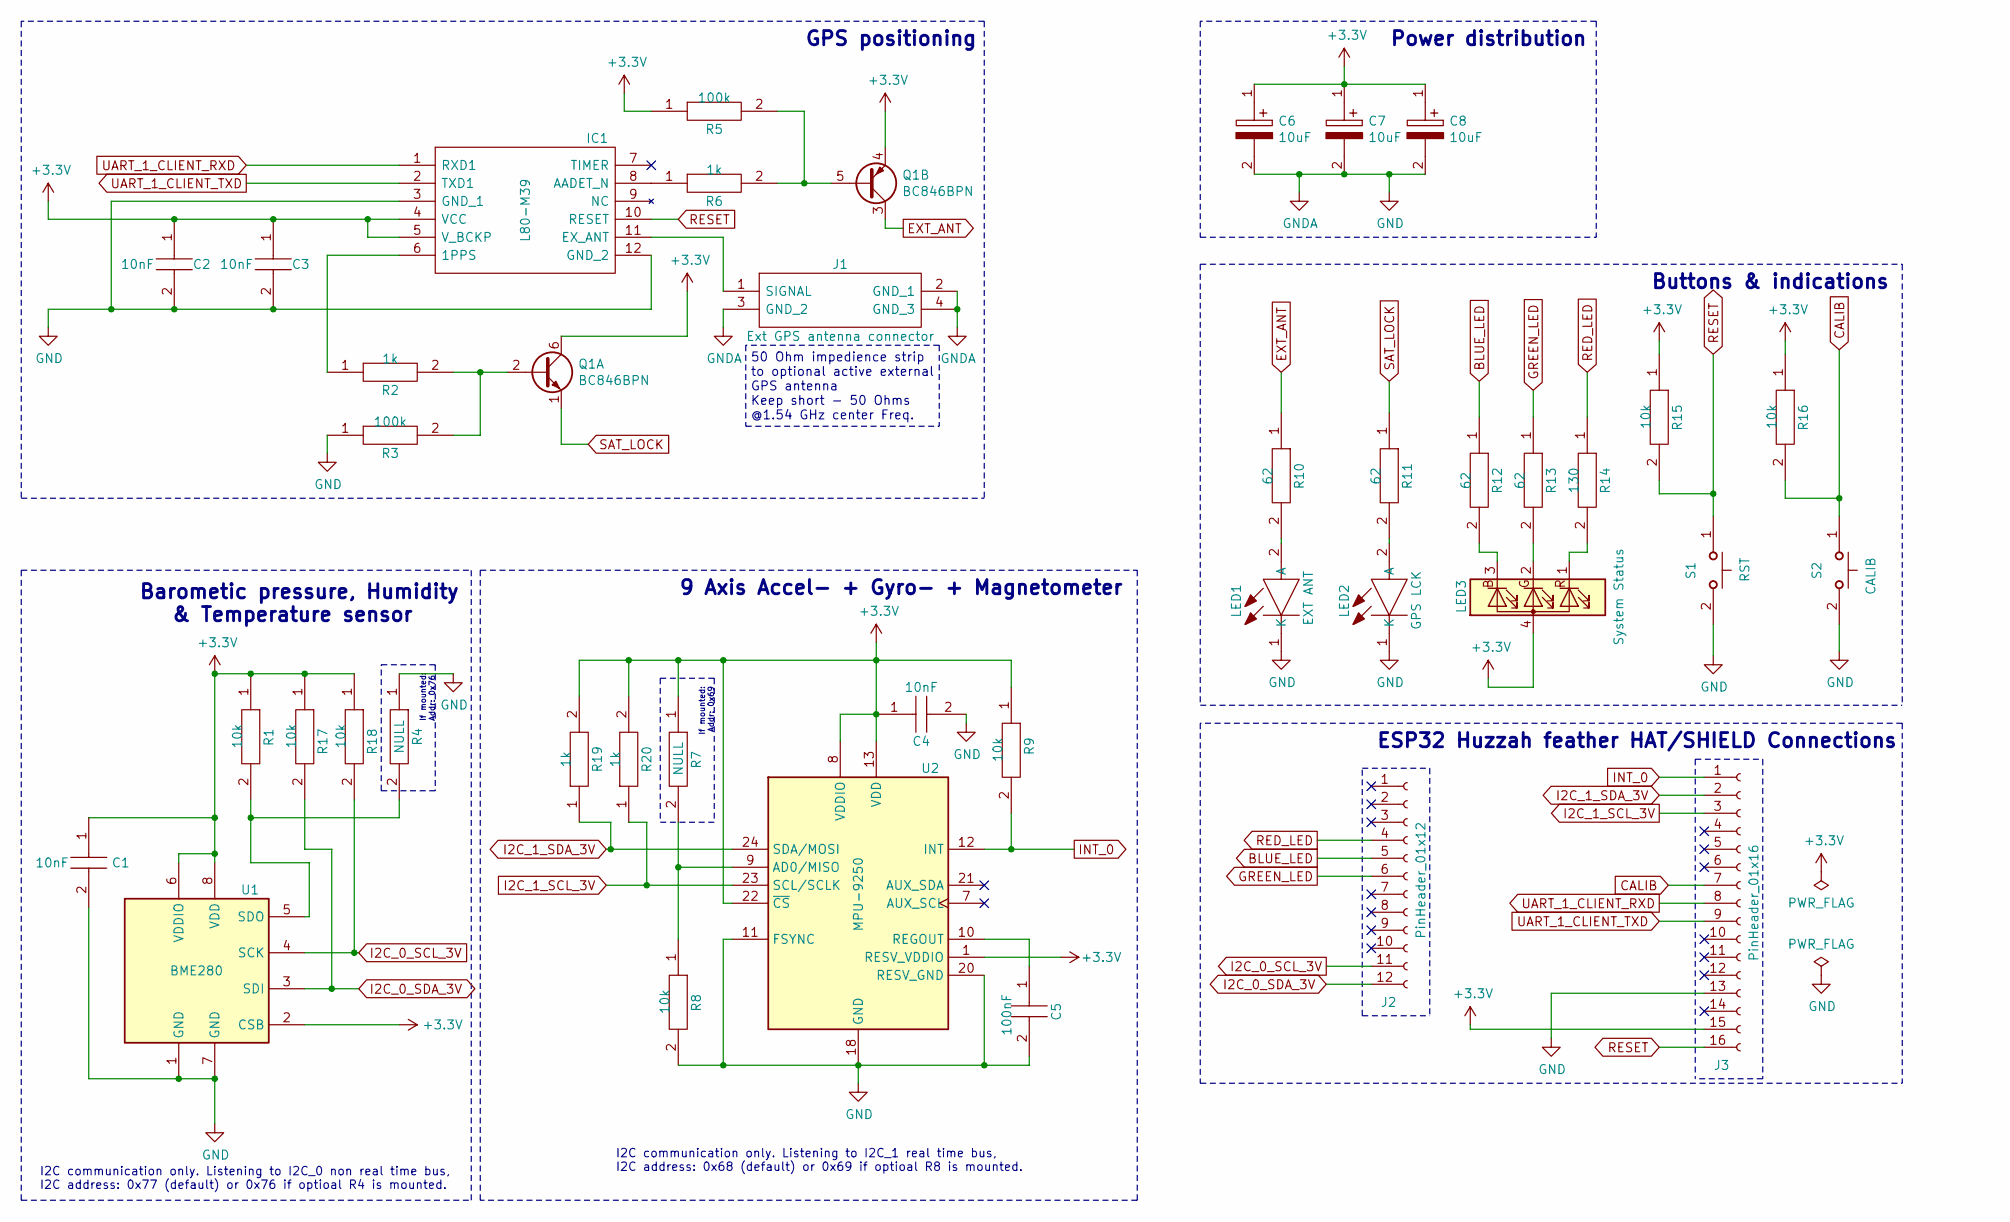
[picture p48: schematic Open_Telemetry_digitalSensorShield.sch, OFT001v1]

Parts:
C1, C2, C3, C4: 10nF; CAPC1608X87N; Manufacturer_Part_Number C0603C103K4RACTU; Mouser Part Number 80-C0603C103K4R
C5: 100nF; CAPC1005X55N; Manufacturer_Part_Number C0402C104M8RACTU; Mouser Part Number 80-C0402C104M8R
C6, C7, C8: 10uF; CAPPM3528X210N; Manufacturer_Part_Number T491B106K016AT7280; Mouser Part Number 80-T491B106K16AT7280
IC1: L80-M39; Manufacturer_Part_Number L80-M39
J1: Ext GPS antenna connector; U.FL_Molex_MCRF_73412-0110_Vertical; Manufacturer_Part_Number 73412-0110; Mouser Part Number 538-73412-0110
J2: PinHeader_01x12; PinHeader_1x12_P2.54mm_Vertical_Down
J3: PinHeader_01x16; PinHeader_1x16_P2.54mm_Vertical_Down
LED1: EXT ANT; LEDC1608X65N; Manufacturer_Part_Number SML-D13DWT86A; Mouser Part Number 755-SML-D13DWT86A
LED2: GPS LCK; SMLD15YWT86; Manufacturer_Part_Number SML-D13FWT86; Mouser Part Number 755-SML-D13FWT86
LED3: System Status; AVAGO_PLCC4
Q1: BC846BPN; SOT-363_SC-70-6
R1, R8, R9, R15, R16, R17, R18: 10k; RESC0603X26N; Manufacturer_Part_Number RC0201JR-0710KL; Mouser Part Number 603-RC0201JR-0710KL
R2, R6, R19, R20: 1k; RESC0603X26N; Manufacturer_Part_Number RC0201JR-071KL; Mouser Part Number 603-RC0201JR-071KL
R3, R5: 100k; RESC0603X26N; Manufacturer_Part_Number RC0201JR-07100KL; Mouser Part Number 603-RC0201JR-07100KL
R4, R7: NULL; RESC0603X26N; Manufacturer_Part_Number RC0201JR-070RL; Mouser Part Number 603-RC0201JR-070RL
R10, R11, R12, R13: 62; RESC1005X40N; Manufacturer_Part_Number RC0402JR-0762RL; Mouser Part Number 603-RC0402JR-0762RL
R14: 130; RESC1005X40N; Manufacturer_Part_Number CRCW0402130RJNED; Mouser Part Number 71-CRCW0402130RJNED
S1: RST; KSR; Manufacturer_Part_Number KSR223GLFG; Mouser Part Number 611-KSR223GLFG
S2: CALIB; KSR; Manufacturer_Part_Number KSR223GLFG; Mouser Part Number 611-KSR223GLFG
U1: BME280; Bosch_LGA-8_2x2.5mm_P0.65mm_ClockwisePinNumbering
U2: MPU-9250; 3DInvenSense_QFN-24_3x3mm_P0.4mm

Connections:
+3V3: C1.1, C2.1, C3.1, C4.1, C6.1, C7.1, C8.1, IC1.4 (VCC), IC1.5 (V_BCKP), J3.15, LED3.4 (A), Q1.4 (E2), Q1.6 (C1), R1.1, R5.1, R7.1, R9.1, R15.1, R16.1, R17.1, R18.1, R19.2, R20.2, U1.2 (CSB), U1.6 (VDDIO), U1.8 (VDD), U2.1 (RESV_VDDIO), U2.8 (VDDIO), U2.13 (VDD), U2.22 (~CS)
BLUE_LED: J2.5, R12.1
CALIB: J3.7, R16.2, S2.1
EXT_ANT: Q1.3 (C2), R10.1
GND: C1.2, C2.2, C3.2, C4.2, C5.2, C6.2, C7.2, C8.2, IC1.3 (GND_1), IC1.12 (GND_2), J1.2 (GND_1), J1.3 (GND_2), J1.4 (GND_3), J3.13, LED1.1 (K), LED2.1 (K), R3.1, R4.1, R8.2, S1.2, S2.2, U1.1 (GND), U1.7 (GND), U2.11 (FSYNC), U2.18 (GND), U2.20 (RESV_GND)
GREEN_LED: J2.6, R13.1
I2C_0_SCL_3V: J2.11, R18.2, U1.4 (SCK)
I2C_0_SDA_3V: J2.12, R17.2, U1.3 (SDI)
I2C_1_SCL_3V: J3.3, R20.1, U2.23 (SCL/SCLK)
I2C_1_SDA_3V: J3.2, R19.1, U2.24 (SDA/MOSI)
INT_0: J3.1, R9.2, U2.12 (INT)
unnamed: C5.1, U2.10 (REGOUT)
unnamed: IC1.6 (1PPS), R2.1
unnamed: IC1.8 (AADET_N), R6.1
unnamed: IC1.11 (EX_ANT), J1.1 (SIGNAL)
unnamed: LED1.2 (A), R10.2
unnamed: LED2.2 (A), R11.2
unnamed: LED3.1 (RK), R14.2
unnamed: LED3.2 (GK), R13.2
unnamed: LED3.3 (BK), R12.2
unnamed: Q1.2 (B1), R2.2, R3.2
unnamed: Q1.5 (B2), R5.2, R6.2
unnamed: R1.2, R4.2, U1.5 (SDO)
unnamed: R7.2, R8.1, U2.9 (AD0/MISO)
RED_LED: J2.4, R14.1
RESET: IC1.10 (RESET), J3.16, R15.2, S1.1
SAT_LOCK: Q1.1 (E1), R11.1
UART_1_CLIENT_RXD: IC1.1 (RXD1), J3.8
UART_1_CLIENT_TXD: IC1.2 (TXD1), J3.9

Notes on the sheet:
ESP32 Huzzah feather HAT/SHIELD Connections
Buttons & indications
Power distribution
GPS positioning
Barometic pressure, Humidity & Temperature sensor
If mounted: Addr: 0x76
If mounted: Addr: 0x69
9 Axis Accel- + Gyro- + Magnetometer
I2C communication only. Listening to I2C_0 non real time bus, I2C address: 0x77 (default) or 0x76 if optioal R4 is mounted.
I2C communication only. Listening to I2C_1 real time bus, I2C address: 0x68 (default) or 0x69 if optioal R8 is mounted.
50 Ohm impedience strip to optional active external GPS antenna Keep short - 50 Ohms @1.54 GHz center Freq.

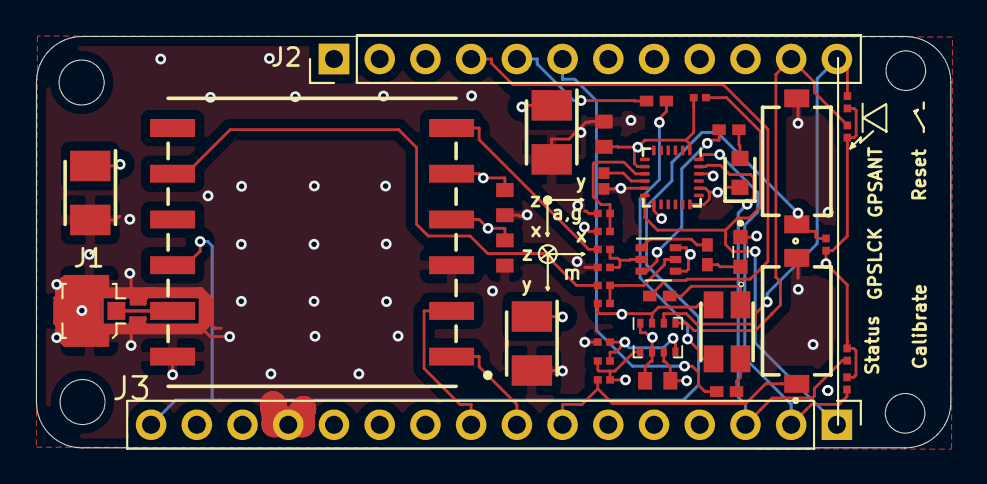
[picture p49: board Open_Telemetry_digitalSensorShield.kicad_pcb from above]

Board: 4 copper layers, 50.8 x 22.9 mm, 44 parts (0 on the bottom side), 29 nets.

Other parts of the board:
P1, P2: MountingHole_2.5mm
P3, P4: MountingHole_2.2mm_M2

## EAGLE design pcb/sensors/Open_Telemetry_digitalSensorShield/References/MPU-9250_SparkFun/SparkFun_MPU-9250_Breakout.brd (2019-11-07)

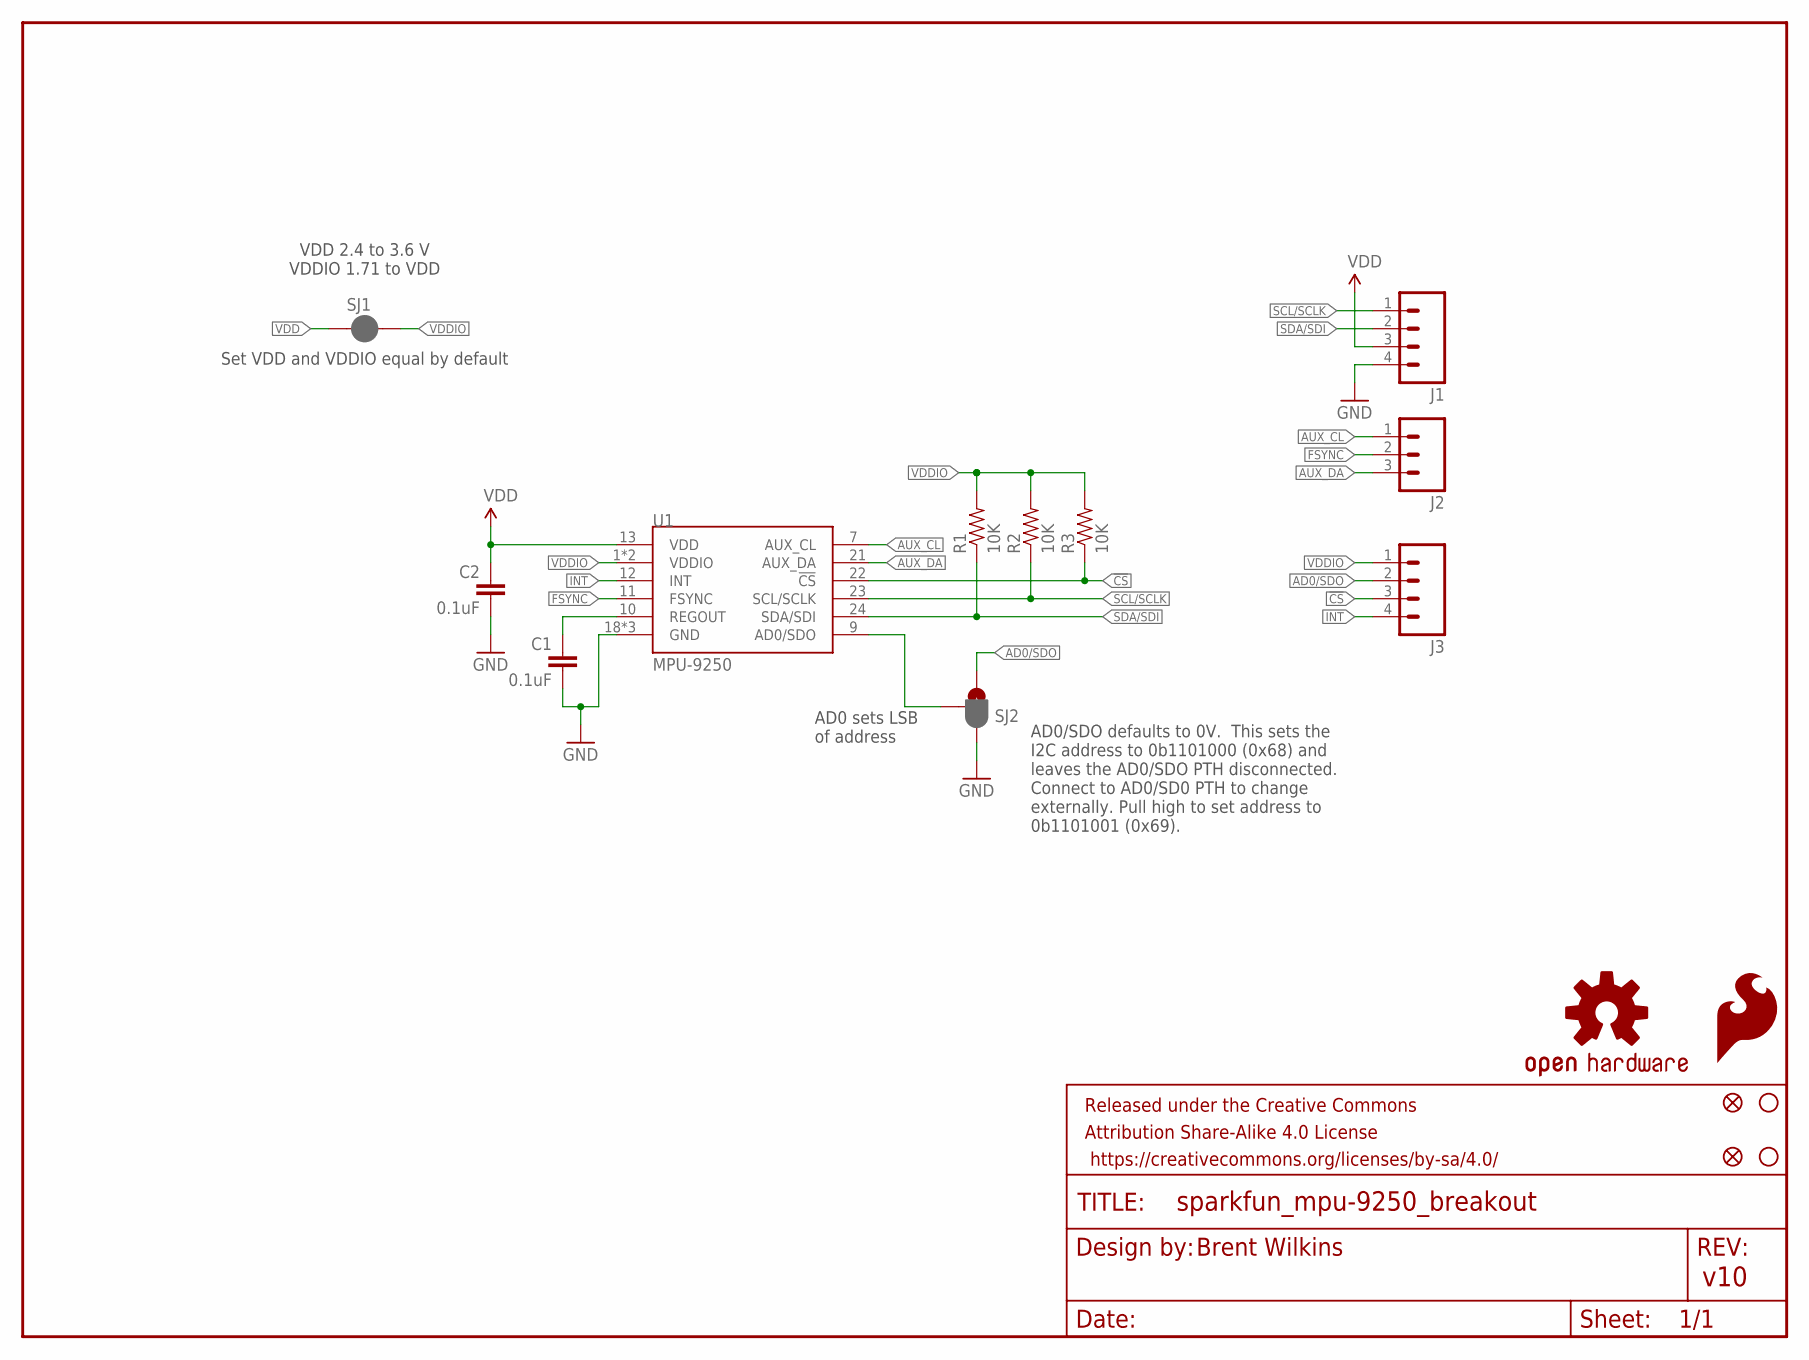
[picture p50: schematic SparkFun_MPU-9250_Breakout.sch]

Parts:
C1, C2: 0.1uF; 0603-CAP
FID1, FID2: FIDUCIAL1X2; FIDUCIAL-1X2
FRAME1: FRAME-LETTER; CREATIVE_COMMONS
J1, J3: M04PTH; 1X04
J2: M03PTH; 1X03
LOGO1: SFE_LOGO_FLAME.1_INCH; SFE_LOGO_FLAME_.1
LOGO2: OSHW-LOGOS; OSHW-LOGO-S
R1, R2, R3: 10K; 0603-RES
SJ1: JUMPER-PAD-2-NC_BY_PASTEFULL-BOX-SILK; PAD-JUMPER-2-NC_BY_PASTE_YES_SILK_FULL_BOX
SJ2: JUMPER_PAD-3-1&2_NC_BY_PASTE; PAD-HUMPER-3-1&2_NC_BY_PASTE_YES_SILK_FULL_BOX
STANDOFF1, STANDOFF2: STAND-OFF
U1: MPU-9250; QFN24_PAD

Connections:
!CS: J3.3, R3.1, U1.22 (!CS)
AD0/SDO: J3.2, SJ2.3
ADSD_STUB: SJ2.2, U1.9 (AD0/SDO)
AUX_CL: J2.1, U1.7 (AUX_CL)
AUX_DA: J2.3, U1.21 (AUX_DA)
FSYNC: J2.2, U1.11 (FSYNC)
GND: C1.2, C2.2, J1.4, SJ2.1, U1.18 (GND), U1.20 (GND), U1.CENTER (GND)
INT: J3.4, U1.12 (INT)
REGOUT: C1.1, U1.10 (REGOUT)
SCL/SCLK: J1.1, R2.1, U1.23 (SCL/SCLK)
SDA/SDI: J1.2, R1.1, U1.24 (SDA/SDI)
VDD: C2.1, J1.3, SJ1.1, U1.13 (VDD)
VDDIO: J3.1, R1.2, R2.2, R3.2, SJ1.2, U1.1 (VDDIO), U1.8 (VDDIO)

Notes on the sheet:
AD0/SDO defaults to 0V. This sets the I2C address to 0b1101000 (0x68) and leaves the AD0/SDO PTH disconnected. Connect to AD0/SD0 PTH to change externally. Pull high to set address to 0b1101001 (0x69).
AD0 sets LSB of address
Set VDD and VDDIO equal by default
VDD 2.4 to 3.6 V VDDIO 1.71 to VDD

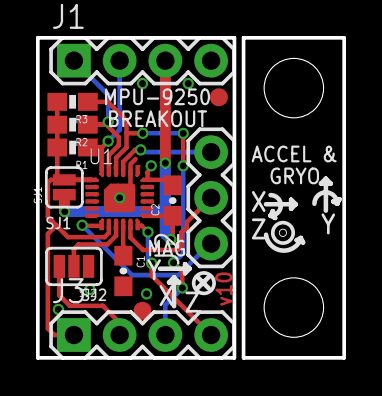
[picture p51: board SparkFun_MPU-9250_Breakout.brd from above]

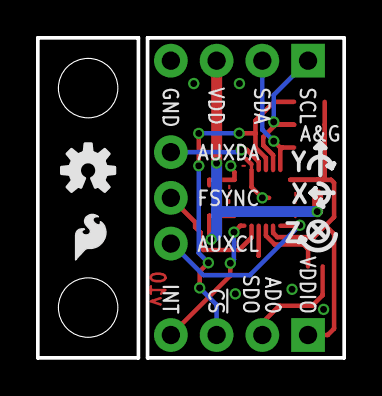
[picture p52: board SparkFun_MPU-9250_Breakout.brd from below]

Board: 2 copper layers, 17.0 x 17.8 mm, 18 parts (2 on the bottom side), 13 nets.

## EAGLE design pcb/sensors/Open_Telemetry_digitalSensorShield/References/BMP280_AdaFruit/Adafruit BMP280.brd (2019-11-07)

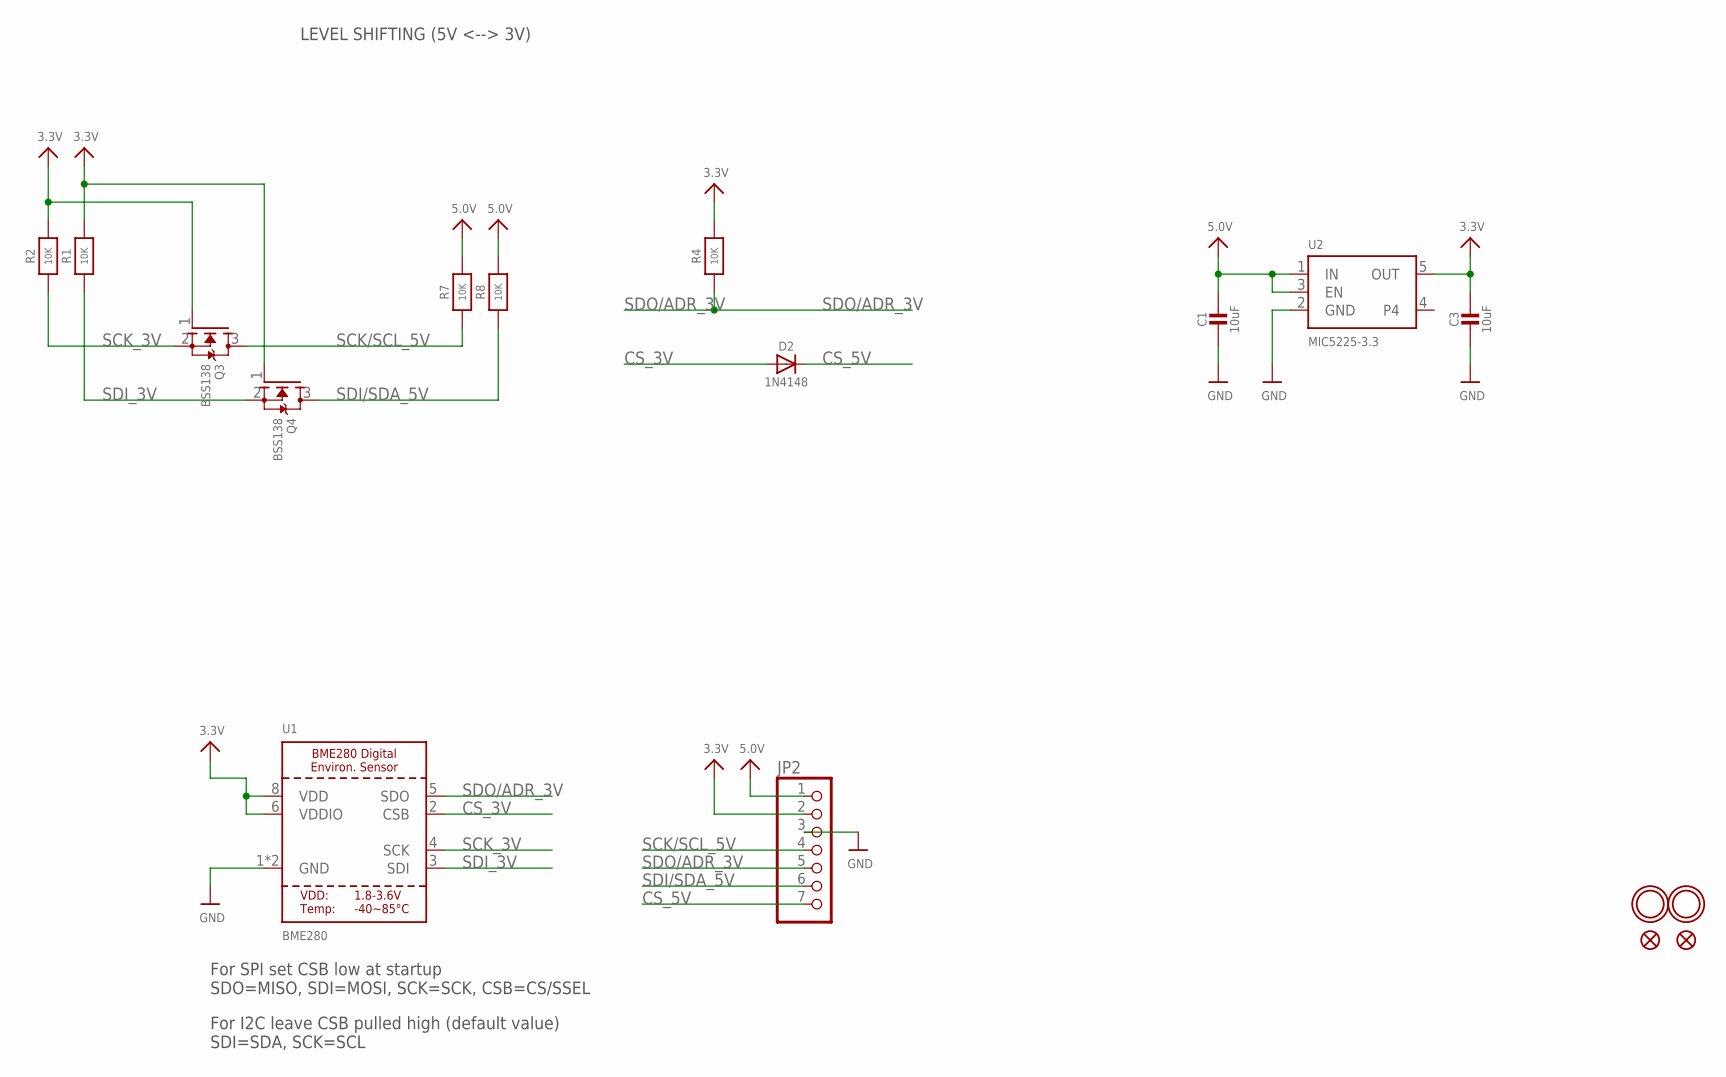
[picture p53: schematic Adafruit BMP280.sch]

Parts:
C1, C3: 10uF; 0805-NO
D2: 1N4148; SOD-323
JP2: HEADER-1X770MIL; 1X07_ROUND_70
Q3, Q4: BSS138; SOT23-WIDE
R1, R2, R7, R8: 10K; 0805-NO
R4: 10K; _0805MP
U1: BME280
U2: MIC5225-3.3; SOT23-5
U$5, U$15: FIDUCIAL""; FIDUCIAL_1MM
U$7, U$8: MOUNTINGHOLE2.0; MOUNTINGHOLE_2.0_PLATED

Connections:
3.3V: C3.1, JP2.2, Q3.1 (G), Q4.1 (G), R1.2, R2.2, R4.2, U1.6 (VDDIO), U1.8 (VDD), U2.5 (OUT)
5.0V: C1.1, JP2.1, R7.2, R8.2, U2.1 (IN), U2.3 (EN)
CS_3V: D2.A, U1.2 (CSB)
CS_5V: D2.C, JP2.7
GND: C1.2, C3.2, JP2.3, U1.1 (GND), U1.7 (GND), U2.2 (GND)
SCK/SCL_5V: JP2.4, Q3.3 (D), R7.1
SCK_3V: Q3.2 (S), R2.1, U1.4 (SCK)
SDI/SDA_5V: JP2.6, Q4.3 (D), R8.1
SDI_3V: Q4.2 (S), R1.1, U1.3 (SDI)
SDO/ADR_3V: JP2.5, R4.1, U1.5 (SDO)

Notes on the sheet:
For SPI set CSB low at startup SDO=MISO, SDI=MOSI, SCK=SCK, CSB=CS/SSEL
For I2C leave CSB pulled high (default value) SDI=SDA, SCK=SCL
LEVEL SHIFTING (5V <--> 3V)

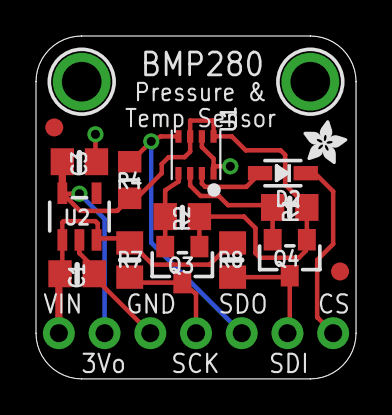
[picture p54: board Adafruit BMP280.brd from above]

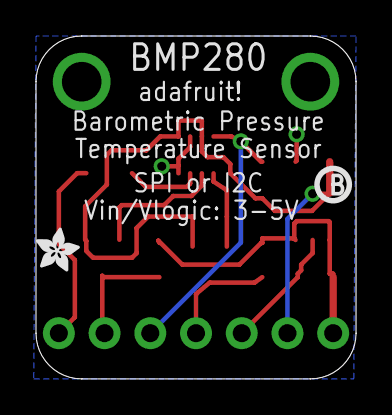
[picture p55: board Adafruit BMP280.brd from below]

Board: 2 copper layers, 17.8 x 19.1 mm, 20 parts (2 on the bottom side), 10 nets.

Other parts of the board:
U$2, U$6: ADAFRUIT_2.5MM
U$20: PCBFEAT-REV-040

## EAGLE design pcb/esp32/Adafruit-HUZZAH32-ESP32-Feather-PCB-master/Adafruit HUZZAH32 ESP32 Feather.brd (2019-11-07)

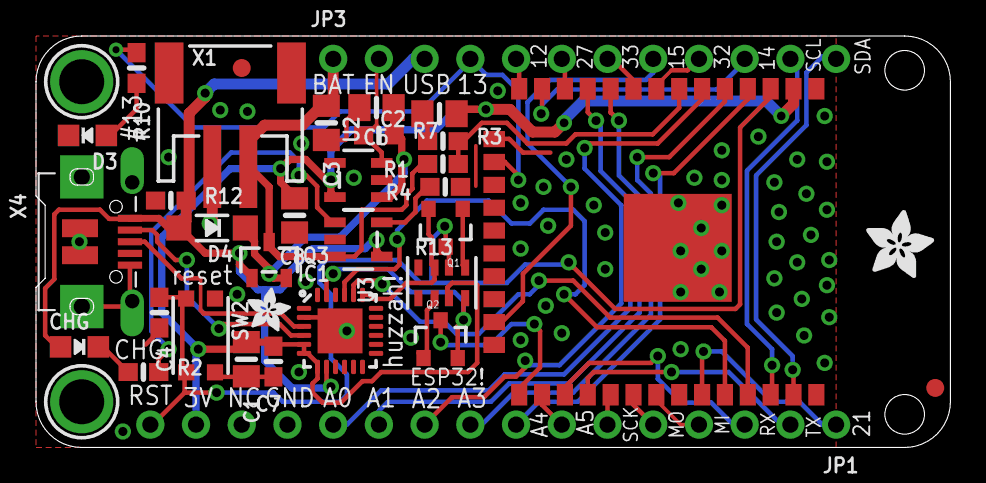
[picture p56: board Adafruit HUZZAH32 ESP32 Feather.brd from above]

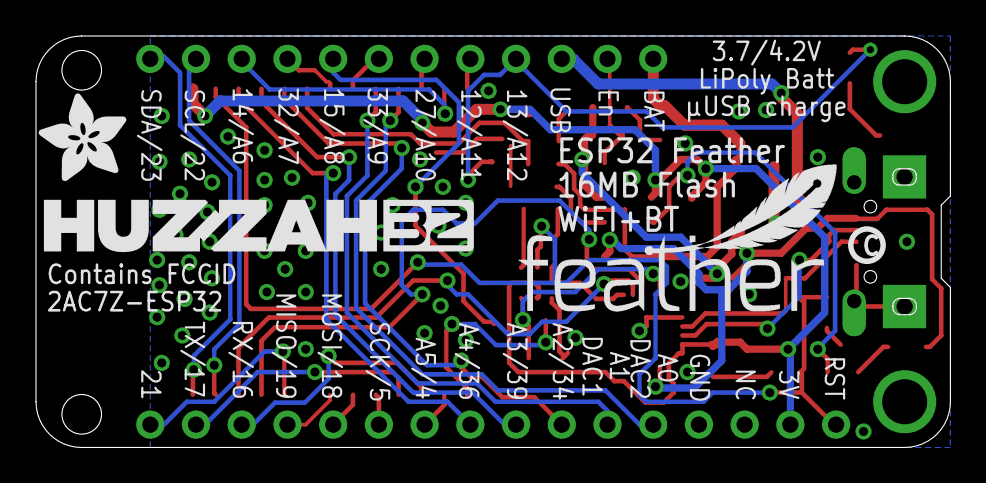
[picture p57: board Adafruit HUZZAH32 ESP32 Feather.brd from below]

Board: 2 copper layers, 50.8 x 22.9 mm, 40 parts (4 on the bottom side), 42 nets.

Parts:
C1, C2: 10uF; 0805-NO
C3, C6, C8: 10µF; 0805-NO
C4, C7: 1uF; 0603-NO
CHG: ORANGE; CHIPLED_0805_NOOUTLINE
D3: RED; CHIPLED_0805_NOOUTLINE
D4: MBR120; SOD-123
IC1: CP2104; QFN24_4MM_SMSC
JP1: 1X16_ROUND_MIN
JP3: 1X12_ROUND_MIN
Q1, Q2: mmbt2222; SOT23-3
Q3: DMG3415U; SOT23-R
R1, R3, R7, R12: 100K; 0603-NO
R2, R10: 1K; 0603-NO
R4: 4.7K; 0603-NO
R13: 10K; RESPACK_4X0603
SW2: KMR2; BTN_KMR2_4.6X2.8
U2: AP2112-3.3; SOT23-5
U3: MCP73831T-2ACI/OT; SOT23-5
U$7: ADAFRUIT_5MM
U$9: FEATHERLOGO_MED
U$13: PCBFEAT-REV-040
U$14: ADAFRUIT_2.5MM
U$15: ADAFRUIT_3.5MM
U$31, U$32: MOUNTINGHOLE2.5; MOUNTINGHOLE_2.5_PLATED
U$34, U$35: FIDUCIAL_1MM
U$43: HUZZAH32
X1: JSTPH; JSTPH2
X2: ESP32_WROOM32_SKINNY; WROOM32_SKINNY
X4: 20329; 4UCONN_20329_V2

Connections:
3.3V: C1.1, C2.1, C7.1, C8.1, IC1.5, IC1.6, IC1.7, JP1.15, R13.3, U2.5, X2.2
A0_DAC2: JP1.12, X2.11
A1_DAC1: JP1.11, X2.10
A2_I34: JP1.10, X2.6
A3_I39: JP1.9, X2.5
A4_IO36: JP1.8, X2.4
A5_IO4: JP1.7, X2.26
A13_I35: R1.1, R3.2, X2.7
DTR: IC1.23, Q2.2, R13.4
EN: JP3.2, R7.1, U2.3
GND: C1.2, C2.2, C3.2, C4.2, C6.2, C7.2, C8.2, D3.C, IC1.2, IC1.THERM, JP1.13, R3.1, R4.1, R12.1, SW2.A, SW2.A', U2.2, U3.2, X1.1, X2.1, X2.15, X2.38, X2.P$1, X4.BASE@1, X4.BASE@2, X4.GND, X4.SPRT@1, X4.SPRT@2, X4.SPRT@3, X4.SPRT@4
GPIO0: Q2.3, X2.25
IO12_A11: JP3.5, X2.14
IO13_A12: JP3.4, R10.1, X2.16
IO14_A6: JP3.10, X2.13
IO15_A8: JP3.8, X2.23
IO16: JP1.3, X2.27
IO17: JP1.2, X2.28
IO21: JP1.1, X2.33
IO27_A10: JP3.6, X2.12
IO32_A7: JP3.9, X2.8
IO33_A9: JP3.7, X2.9
MISO: JP1.4, X2.31
MOSI: JP1.5, X2.30
unnamed: CHG.C, R2.1
unnamed: IC1.3, X4.D+
unnamed: R2.2, U3.1
unnamed: R4.2, U3.5
unnamed: D3.A, R10.2
unnamed: IC1.4, X4.D-
unnamed: C6.1, D4.C, Q3.2, R7.2, U2.1
unnamed: Q1.1, R13.5
unnamed: Q2.1, R13.2
RESET: C4.1, JP1.16, Q1.3, R13.6, SW2.B, SW2.B', X2.3
RTS: IC1.19, Q1.2, R13.7
RXD0: IC1.21, X2.34
SCK: JP1.6, X2.29
SCL: JP3.11, X2.36
SDA: JP3.12, X2.37
TXD0: IC1.20, X2.35
VBAT: C3.1, JP3.1, Q3.3, R1.2, U3.3, X1.2
VBUS: CHG.A, D4.A, IC1.8, JP3.3, Q3.1, R12.2, U3.4, X4.VBUS

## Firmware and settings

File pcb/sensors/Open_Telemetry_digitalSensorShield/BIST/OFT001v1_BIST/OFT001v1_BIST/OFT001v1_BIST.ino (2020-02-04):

/* ************************************************************************************************* *
 * (c) Copyright 2020 Jonas Bjurel (jonasbjurel@hotmail.com)                                         *
 *                                                                                                   *
 * Licensed under the Apache License, Version 2.0 (the "License");                                   *
 * you may not use this file except in compliance with the License.                                  *
 * You may obtain a copy of the License at http://www.apache.org/licenses/LICENSE-2.0                *
 *                                                                                                   *
 * Unless required by applicable law or agreed to in writing, software distributed under the License *
 * is distributed on an "AS IS" BASIS, WITHOUT WARRANTIES OR CONDITIONS OF ANY KIND, either express- *
 * or implied.                                                                                       *
 * See the License for the specific language governing permissions and limitations under the         *
 * licence.                                                                                          *
 *                                                                                                   *
 * ************************************************************************************************* */

 /* ************************************************************************************************* *
  * Project:		    openTelemetryHW - https://github.com/jonasbjurel/open_telemetry_HW            *
  * Name:				OFT001V1 P1A BIST (Built in Self test program)                                *
  * Created:			2020-01-18                                                                    *
  * Originator:			Jonas Bjurel (jonasbjurel@hotmail.com)                                        *
  * Short description:	Provides a Built in self-test program for the OFT 001 V1 P1A board:           *
  *                     Following features are provided:                                              * 
  *                     o Discovery and callibration of all board functions such as                   *
  *                        - Buttons                                                                  *
  *                        - LED Luminances                                                               *
  *                        - BMP280 Barometic and temperature data                                    *
  *                        - MPU9250 9-axis intertial navigation sensor                               *
  *                        - L80-M39 GPS receiver                                                     *
  *                    o Sample streaming of navigational data to part Kalman filtered, such as:      *
  *                        - Euler angels and Euler angles change rates                               *
  *                        - Barometic pressure and Barometic vaiometering (bar alt change rates)     *
  *                   	   - GPS positioning, hight and GPS variometer (GPS alt change rates)         *
  *                        - Magnetic fields-, heading-, inclination-, heading chage-rate, etc...     *
  *																									  *
  *                   THIS CODE IS ONLY FOR SELF TEST OF THE OFT001v1 MODULE, and as reference what   *
  *                   you may be doing wth that module, it is not a good practice of production code, *
  *                   it is not a beuiuty well structured code - but it works for what it was built   *
  *                   for .....                                                                       *
  * Resources:        https://github.com/jonasbjurel/open_telemetry_HW                                                           *
  * ************************************************************************************************* */

/* ****************************************************************************************************
   Libray inclutions                                                                                  *
You need to follow this instruction to get needed libraries included to your project                  *
***************************************************************************************************** */
#include <EEPROM.h>
#include <BLEDevice.h>
#include <dummy.h>
#include "Arduino.h"
#include <math.h> 
#include <stdio.h>
#include <Wire.h>
#include <SPI.h>
#include <Adafruit_BMP280.h>
#include <MPU9250.h>
#include <Adafruit_GPS.h>
#include <BLEDevice.h>
#include <BLEServer.h>
#include <BLEUtils.h>
#include <BLE2902.h>
#include <string.h>
#include <math.h>
#include <stdio.h>
#include "esp_attr.h"
//#include <SoftwareSerial.h> //maybe we should use Soft serial for the GPS as other more critical 
                              // task may need the few HW serials available - more likely we will use
                              // a I2C for S.Port and SmartPort?
/* End Libray inclutions                                                                              *
***************************************************************************************************** */

/* ****************************************************************************************************
   ESP32 Huzza Feather PIN definitions (ESP32 Wroom)                                                  *
***************************************************************************************************** */
#define CALIB_PIN  4
#define RED_LED_PIN 13
#define BLUE_LED_PIN 12
#define GREEN_LED_PIN 27
#define I2C_0_SCL_PIN 22
#define I2C_0_SDA_PIN 23
#define I2C_1_SCL_PIN 16
#define I2C_1_SDA_PIN 17
#define GPS_SERIAL_TXD_PIN 25
#define GPS_SERIAL_RXD_PIN 39
#define MPU_INTERRUPT_PIN 21
/* End ESP32 Huzza Feather PIN definitions                                                            *
***************************************************************************************************** */

/* ****************************************************************************************************
   I/F and device object definitions                                                                  *
***************************************************************************************************** */
#define BMP280_ADDR 0x77
#define BMP280_CID 0x58
#define MPU9250_ADDR 0x68
TwoWire I2C_0 = TwoWire(0); // I2C_0, Common non-critical I2C
TwoWire I2C_1 = TwoWire(1); // I2C_0, MPU dedicated critical I2C
#define GPSSerial Serial2
Adafruit_BMP280 bmp(&I2C_0);
MPU9250 mpu;
Adafruit_GPS GPS(&GPSSerial);
/* End I/F and device object definitions                                                              *
***************************************************************************************************** */

/* ****************************************************************************************************
   Register addresses and common register contents                                                    *
***************************************************************************************************** */

#define MPU9250_INT_PIN_CFG_ADDR 0x37
/* MPU9250_INT_PIN_CFG Register description
Bit-wise functions [7]MSB, [0]LSB
[7] ACTL
    1 – The logic level for INT pin is active low.
    0 – The logic level for INT pin is active high.
[6] OPEN
    1 – INT pin is configured as open drain.
    0 – INT pin is configured as push - pull.
[5] LATCH_INT_EN
    1 – INT pin level held until interrupt status is cleared.
    0 – INT pin indicates interrupt pulse’s is width 50us.
[4] INT_ANYRD_2CLEAR
    1 – Interrupt status is cleared if any read operation is performed.
    0 – Interrupt status is cleared only by reading INT_STATUS register
[3] ACTL_FSYNC
    1 – The logic level for the FSYNC pin as an interrupt is active low.
	0 – The logic level for the FSYNC pin as an interrupt is active high.
[2] FSYNC_INT_MODE_EN
    1 – This enables the FSYNC pin to be used as an interrupt. A transition to the active level described by the ACTL_FSYNC bit 
	    will cause an interrupt. The status of the interrupt is read in the I2 C Master Status register PASS_THROUGH bit.
	0 – This disables the FSYNC pin from causing an interrupt.
[1] BYPASS_EN
    1 - When asserted, the i2c_master interface pins(ES_CL and ES_DA) will go into ‘bypass mode’ when the i2c master interface is
	    disabled.The pins will float high due to the internal pull - up if not enabled and the i2c master interface is disabled.
[0] RESERVED
*/

#define MPU9250_INT_PIN_CFG_DRAIN_HIGH_LATCH 0x60 //0110 0000
#define MPU9250_INT_PIN_CFG_DRAIN_LOW_LATCH 0xE0  //1110 0000
#define MPU9250_INT_PIN_CFG_DEFAULT 0x00

#define MPU9250_INT_ENABLE_ADDR 0x38
/* MPU9250_INT_ENABLE Register description
Bit-wise functions [7]MSB, [0]LSB
[7] RESERVED
[6] WOM_EN
    1 – Enable interrupt for wake on motion to propagate to interrupt pin.
	0 – function is disabled.
[5] RESERVED
[4] FIFO_OVERFLOW_EN
    1 – Enable interrupt for fifo overflow to propagate to interrupt pin.
	0 – function is disabled.
[3] FSYNC_INT_EN
    1 – Enable Fsync interrupt to propagate to interrupt pin.
	0 – function is disabled. 
[2] RESERVED
[1] RESERVED
[0] RAW_RDY_EN
    1 – Enable Raw Sensor Data Ready interrupt to propagate to interrupt pin.
	    The timing of the interrupt can vary depending on the setting in register 36 I2C_MST_CTRL, bit [6] WAIT_FOR_ES.
	0 – function is disabled.
*/
#define MPU9250_INT_EN_DATA_READY 0x01 //00000001
#define MPU9250_INT_DISABLE 0x00

#define MPU9250_INT_STATUS 0x3A
/* MPU9250_INT_STATUS Register description
Bit-wise functions [7]MSB, [0]LSB
[7] Reserved
[6] WOM_INT
    1 – Wake on motion interrupt occurred.
[5] Reserved
[4] FIFO_OVERFLOW_INT
    1 – Fifo Overflow interrupt occurred.  Note that the oldest data is has been dropped from the fifo. 
[3] FSYNC_INT 
    1 – Fsync interrupt occurred. 
[2] Reserved
[1] Reserved
[0] RAW_DATA_RDY_INT
    1 – Sensor Register Raw Data sensors are updated and Ready to be read. The timing of the interrupt can vary depending on the setting in register 36
	   I2C_MST_CTRL, bit [6] WAIT_FOR_ES. 
*/
#define RAW_DATA_RDY_INT_SRC_MASK 0x01 //00000001
#define RAW_DATA_RDY(INT_STATUS) (INT_STATUS & RAW_DATA_RDY_INT_SRC_MASK)
/* END - Register addresses and common register contents                                              *
***************************************************************************************************** */

/* ****************************************************************************************************
   BIST testphases and reult codes                                                                    *
***************************************************************************************************** */ 
//Major BIST test phases
#define START_TEST 0
#define CALIB_BUTTON_TEST 1
#define STATUS_LED_TEST 2
#define BMP280_TEST 3
#define MPU9250_TEST 4
#define L80M39_TEST 5
#define SUCCESS_TEST 253
#define STREAM_SENSORDATA_TEST 254
#define FAIL_TEST 255
int testPhase = START_TEST;
int subTestPhase = 0;

//BIST Fault codes
#define BIST_FC_SUCCESS 0
#define BIST_FC_CALIB_BUTTON_FAIL 1
#define BIST_FC_STATUS_LED_FAIL 2
#define BIST_FC_BPM280_NO_DETECT_FAIL 3
#define BIST_FC_BPM280_DETECT_BUT_NO_FUNCTION_FAIL 4
#define BIST_FC_L80M39_NO_DETECT_FAIL 5
#define BIST_FC_L80M39_DETECT_BUT_NO_FUNCTION_FAIL 6
#define BIST_FC_GPS_NO_1PSS_LOCK_FAIL 7
#define BIST_FC_NO_EXT_ANT_DETECT_FAIL 8
#define BIST_FC_MPU9250_NO_DETECT_FAIL 9
#define BIST_FC_AK8963_NO_DETECT_FAIL 10
#define BIST_FC_MPU9250_DETECT_BUT_NO_FUNCTION_FAIL 10
#define BIST_FC_MPU9250_INTERUPT_LINE_OPEN 11
#define BIST_FC_MPU9250_NO_INTERUPT 12
int bistFc = BIST_FC_SUCCESS;
char calibTextVal[10];
uint8_t mpuInterruptReceived = 0;

/* End BIST testphases and reult codes                                                                *
***************************************************************************************************** */

/* ****************************************************************************************************
   Callib button and Status led definitions                                                           *
***************************************************************************************************** */
//Needs to be refactores - unstructured defininitions below...
unsigned long timeout = 0;
int statusLedPhase = 0;
int ledColorCalib = 0;
int ledTestDelay = 2000;
int ledTestCnt = 0;
const int freq = 5000;
const int resolution = 12;
const int RED_LED_CH = 0;
const int BLUE_LED_CH = 1;
const int GREEN_LED_CH = 2;
int ledRedLuminance = 41; //1% of max is safe
int ledBlueLuminance = 41;
int ledGreenLuminance = 41;
int calibDebounce = 0;

/* ****************************************************************************************************
   BMP280 Barometic and Temp definitions                                                              *
***************************************************************************************************** */
//Calibration data

//Output Variables
float temp;
float barPres;
float barPresCalib;
float barAlt;
float barVar;

//Output Txt presentation
char barPresTxt[10] = "----.-";
char barAltTxt[10] = "+--.-";
char barVarTxt[10] = "+--.-";
char tempTxt[10] = "+--.-";
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
void loop() {
	switch (testPhase) {
	//BIST First introductionary test phase
	case START_TEST:
		consolePrintln("Selftest test for OpenFlightTelemetry OFT001v1 board");
		Serial.print("Xtensa architecture ESP32 CPU running @: ");
		Serial.print(ESP.getCpuFreqMHz());
		Serial.println("MHz");
		consolePrint("press  calibration button to continue .");
		timeout++;
		delay(1000);
		testPhase++;
		subTestPhase = 0;
		break;

	//BIST Testing the Callib button
	case CALIB_BUTTON_TEST:
		if (digitalRead(CALIB_PIN)) {
			consolePrint(".");
			if (timeout >= 20) {
				consolePrintln("");
				consolePrintln("Self test FAILED - Calibration button not working - FAIL");
				timeout = 0;
				bistFc = BIST_FC_CALIB_BUTTON_FAIL;
				testPhase = FAIL_TEST;
			}
			else {
				consolePrint(".");
				timeout++;
				delay(1000);
			}
		}
		else {
			consolePrintln("");
			consolePrintln("Calibration button push detected - SUCCESS");
			ledRedLuminance = 0;
			ledBlueLuminance = 0;
			ledGreenLuminance = 0;
			timeout = 0;
			calibDebounce = 1;
			testPhase++;
			subTestPhase = 0;
		}
		break;

	//BIST Testing and callibrating LEDs
	case STATUS_LED_TEST:
		if (calibDebounce && !digitalRead(CALIB_PIN)) {
			break;
		}
		if (calibDebounce && digitalRead(CALIB_PIN)) {
			calibDebounce = 0;
		}
		switch (ledColorCalib) {
		case 0:
			if (!ledRedLuminance)
				consolePrintln("Calibrating status LEDs, starting with RED, press the calibration button when satisfied with the Luminance");

			if (!digitalRead(CALIB_PIN) || (ledRedLuminance >= pow(2, resolution))) {
				consolePrint("RED led is calibrated to: ");
				gcvt((100 * ledRedLuminance / pow(2, resolution)), 2, calibTextVal);
				consolePrint(calibTextVal);
				consolePrintln(" %");
				ledColorCalib++;
				calibDebounce = 1;
				delay(1000);
			}
			else {
				ledRedLuminance++;
				ledcWrite(RED_LED_CH, (pow(2, resolution) - ledRedLuminance));
				delay(100);
			}
			break;
		case 1:
			if (!ledBlueLuminance) {
				consolePrintln("Continuing with BLUE, press the calibration button when satisfied with the Luminance");
			}
			if (!digitalRead(CALIB_PIN) || (ledBlueLuminance >= pow(2, resolution))) {
				consolePrint("BLUE led is calibrated to: ");
				gcvt((100 * ledBlueLuminance / pow(2, resolution)), 2, calibTextVal);
				consolePrint(calibTextVal);
				consolePrintln(" %");
				ledColorCalib++;
				calibDebounce = 1;
				delay(1000);
				ledcWrite(BLUE_LED_CH, (pow(2, resolution) - 0));
			}
			else {
				ledBlueLuminance++;
				if (ledBlueLuminance & 2) {
					ledcWrite(RED_LED_CH, (pow(2, resolution) - 0));
					ledcWrite(BLUE_LED_CH, (pow(2, resolution) - ledBlueLuminance));
				}
				else {
					ledcWrite(BLUE_LED_CH, (pow(2, resolution) - 0));
					ledcWrite(RED_LED_CH, (pow(2, resolution) - ledRedLuminance));
				}
				delay(100);
			}
			break;
		case 2:
			if (!ledGreenLuminance) {
				consolePrintln("Continuing with GREEN, press the calibration button when satisfied with the Luminance");
			}
			if (!digitalRead(CALIB_PIN) || (ledGreenLuminance >= pow(2, resolution))) {
				consolePrint("GREEN led is calibrated to: ");
				gcvt((100 * ledGreenLuminance / pow(2, resolution)), 2, calibTextVal);
				consolePrint(calibTextVal);
				consolePrintln(" %");
				ledColorCalib++;
				delay(1000);
				ledcWrite(GREEN_LED_CH, (pow(2, resolution) - 0));
				ledcWrite(RED_LED_CH, (pow(2, resolution) - 0));
			}
			else {
				ledGreenLuminance++;
				if (ledGreenLuminance & 2) {
					ledcWrite(RED_LED_CH, (pow(2, resolution) - 0));
					ledcWrite(GREEN_LED_CH, (pow(2, resolution) - ledGreenLuminance));
				}
				else {
					ledcWrite(GREEN_LED_CH, (pow(2, resolution) - 0));
					ledcWrite(RED_LED_CH, (pow(2, resolution) - ledRedLuminance));
				}
				delay(100);
			}
			break;
		case 3:
			ledcWrite(RED_LED_CH, (pow(2, resolution) - 0));
			ledcWrite(BLUE_LED_CH, (pow(2, resolution) - 0));
			ledcWrite(GREEN_LED_CH, (pow(2, resolution) - 0));
			if (ledTestCnt++ > 1) ledTestCnt = 0;
			switch (ledTestCnt) {
			case 0:
				ledcWrite(BLUE_LED_CH, (pow(2, resolution) - 0));
				ledcWrite(RED_LED_CH, (pow(2, resolution) - ledRedLuminance));
				break;
			case 1:
				ledcWrite(RED_LED_CH, (pow(2, resolution) - 0));
				ledcWrite(BLUE_LED_CH, (pow(2, resolution) - ledBlueLuminance));
				break;
			case 2:
				ledcWrite(BLUE_LED_CH, (pow(2, resolution) - 0));
				ledcWrite(GREEN_LED_CH, (pow(2, resolution) - ledGreenLuminance));
				break;
			}
			delay(ledTestDelay);
			ledTestDelay = ledTestDelay * 0.8;
			if (ledTestDelay < 2) {
				ledcWrite(RED_LED_CH, (pow(2, resolution) - ledRedLuminance));
				ledcWrite(BLUE_LED_CH, (pow(2, resolution) - ledBlueLuminance));
				ledcWrite(GREEN_LED_CH, (pow(2, resolution) - ledGreenLuminance));
				delay(1000);
				ledcWrite(RED_LED_CH, (pow(2, resolution) - 0));
				ledcWrite(BLUE_LED_CH, (pow(2, resolution) - ledBlueLuminance));
				ledcWrite(GREEN_LED_CH, (pow(2, resolution) - 0));
				testPhase++;
				subTestPhase = 0;
			}
			break;
		}
		break;

	//BIST Testing the BMP280 barometic and temperature sensor
	case BMP280_TEST:
		if (!bmp.begin(BMP280_ADDR, BMP280_CID)) {
			consolePrintln("Self test FAILED - BMP280 Barometic sensor NOT found - FAIL");
			bistFc = BIST_FC_BPM280_NO_DETECT_FAIL;
			testPhase = FAIL_TEST;
		}
		else {
			consolePrintln("BMP280 Barometic sensor found - SUCCESS");
			bmp.setSampling(Adafruit_BMP280::MODE_NORMAL, /* Operating Mode.        */
				Adafruit_BMP280::SAMPLING_X2,             /* Temp. oversampling     */
				Adafruit_BMP280::SAMPLING_X16,            /* Pressure oversampling  */
				Adafruit_BMP280::FILTER_OFF,              /* Filtering.             */
				Adafruit_BMP280::STANDBY_MS_500);         /* Standby time.          */
			testPhase++;
			subTestPhase = 0;
		}
		break;

	//BIST Testing the MPU9250 inertial sensor
	case MPU9250_TEST:
		switch (subTestPhase) {
		case 0:
			mpu.setup(I2C_1);
			delay(1000);
			if (mpu.isConnectedMPU9250()) {
				//mpu.setMagneticDeclination(0);
				consolePrintln("MPU9250 6 axis inertial sensor found - SUCCESS");
				delay(5000);
				subTestPhase++;
			}
			else { 
				consolePrintln("MPU9250 6 axis inertial sensor NOT found -  FAIL");
				bistFc = BIST_FC_MPU9250_NO_DETECT_FAIL;
				testPhase = FAIL_TEST;
			}
			break;
		case 1:
			if (mpu.isConnectedAK8963()) {
				consolePrintln("AK8963 3 axis magnetometer found - SUCCESS");
				subTestPhase++;
			}
			else {
				consolePrintln("AK8963 3 axis magnetometer NOT found - FAIL");
				bistFc = BIST_FC_AK8963_NO_DETECT_FAIL;
				testPhase = FAIL_TEST;
			}
			break;
		case 2:
			consolePrintln("Checking MPU9250 Interrupt line LOW without MPU9250 interrupts enabled - to detact a broken interrupt line (OFT has a pull-up)...");
			//attachInterrupt(MPU_INTERRUPT_PIN, gotMpuInterrupt, GPIO_INTR_LOW_LEVEL);
			mpuInterruptTimeout = millis() + 1000;
			subTestPhase++;
			break;
		case 3:
			if (mpuInterruptReceived) {
				detachInterrupt(MPU_INTERRUPT_PIN);
				consolePrintln("Spurious MPU9250 Interrupt received while it shouldnt have/was not programed to generate interupts - FAIL");
				bistFc = BIST_FC_MPU9250_INTERUPT_LINE_OPEN;
				testPhase = FAIL_TEST;
			}
			else {
				if (millis() > mpuInterruptTimeout) {
					consolePrintln("No spurious MPU9250 Interrupt received - SUCCESS");
					consolePrintln("Checking MPU9250 Interrupt line rising edge with MPU9250 programmed to generate Interrupts(RISING EDGE) when data is available...");
					mpuInterruptReceived = 0;
					detachInterrupt(MPU_INTERRUPT_PIN);
					mpu.write(MPU9250_INT_PIN_CFG_ADDR, MPU9250_INT_PIN_CFG_DEFAULT);
					delay(100);
					mpu.write(MPU9250_INT_ENABLE_ADDR, MPU9250_INT_EN_DATA_READY);
					delay(100);
					attachInterrupt(MPU_INTERRUPT_PIN, gotMpuInterrupt, GPIO_INTR_POSEDGE);
					mpu.read(MPU9250_ADDR, MPU9250_INT_STATUS);
					mpuInterruptTimeout = millis() + 1000;
					subTestPhase++;
				}
			}
			break;
		case 4:
			if (mpuInterruptReceived) {
				detachInterrupt(MPU_INTERRUPT_PIN);
				consolePrintln("MPU9250 Interrupt received as it should - SUCCESS");
				mpu.write(MPU9250_INT_ENABLE_ADDR, MPU9250_INT_DISABLE);
				testPhase++;
				subTestPhase = 0;
			}
			else {
				if (millis() > mpuInterruptTimeout) {
					detachInterrupt(MPU_INTERRUPT_PIN);
					consolePrintln("No MPU9250 Interrupt received - FAIL");
					mpu.write(MPU9250_INT_ENABLE_ADDR, MPU9250_INT_DISABLE);
					bistFc = BIST_FC_MPU9250_NO_INTERUPT;
					testPhase = FAIL_TEST;
				}
			}
			break;
		}
		break;
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

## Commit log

2019-11-07 First version of the digital sensor board routed.
    [20041.stp, 70522025.stp, 70522027.stp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]
2019-11-12 2'nd internal review
    [CRCW0402130RJNED.stl, CRCW0402130RJNED.stp, EDI2CAP.CFG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]
2019-11-15 OFT001v1 Inertial HW board ready for internal review. Find it underpcb/sensors/Open_Telemetry_digitalSensorShield/...
    [Adafruit BMP280.brd, Adafruit BMP280.sch, Compoonent quotes.xlsx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]
2019-11-18 First candidate for prototype manufacturing of OFT001 P1A01 sent to PCBWay after a early feedback. Close to manufacturing goahead.
    [Compoonent quotes.xlsx, EDI2CAP.CFG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]
2019-11-19 This was suposed to be the last commit going into P1A prototype manufacturing, but there are likely missing pull-ups for the 2 I2C busses needing correction. Probably a 1k pullup for the high speed M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
2019-11-20 P1A02 files sent to manufactuing review. Added R17, R18, R19, RR20 I2C pullups for reliability and hiher speeds.
    [Open_Telemetry_digitalSensorShield-B_Adhes.gbr, Open_Telemetry_digitalSensorShield-B_CrtYd.gbr, Open_Telemetry_digitalSensorShield-B_Cu.gbr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]
2019-11-21 Corrected the PCBWAY BOM
    [W32271ASH4-5sets-Open_Telemetry_digitalSensorShieldBOM_PCBWay.xlsx]
2019-11-21 Added picture for patch antenna char
2019-12-12 Corrected the error where BME280 was placed as U1 instead of BMP280 This is the baseline that will be delivered as the P1A prototype card.
    [Open_Telemetry_digitalSensorShield.sch, Open_Telemetry_digitalSensorShieldBOM_Generic.xlsx, W32271ASH4-5sets-Open_Telemetry_digitalSensorShieldBOM_PCBWay.xlsx]
2020-01-20 First BIST Self-test ESP32 program for the OFT001V1 P1A module - not elegant - but working it's purpose to evaluate the sensor module - which it does fine!
2020-01-25 Fixed OFT001v1 BIST GPS reading issues
    [OFT001v1_BIST.ino]
2020-02-04 BIST library dependencies explisitly added to the repository. A few BIST bugs fixed.
    [OFT001v1_BIST.ino]

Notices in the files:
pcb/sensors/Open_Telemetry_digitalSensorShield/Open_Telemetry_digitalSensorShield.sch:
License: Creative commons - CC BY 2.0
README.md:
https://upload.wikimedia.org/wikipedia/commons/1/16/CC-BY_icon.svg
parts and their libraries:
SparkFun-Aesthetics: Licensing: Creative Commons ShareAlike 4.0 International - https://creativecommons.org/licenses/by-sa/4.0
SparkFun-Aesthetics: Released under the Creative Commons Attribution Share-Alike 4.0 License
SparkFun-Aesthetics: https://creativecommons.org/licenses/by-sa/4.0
